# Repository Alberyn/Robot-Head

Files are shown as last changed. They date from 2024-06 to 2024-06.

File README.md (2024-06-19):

# Robot-Head
### Исследование
**Цели и задачи** - Проектирование насадки на роборуку Omron tm5-700.
Перед нами была поставлена задача проектирования, создания и симуляции насадки для роборуки. В процессе поисков вариантов и согласования идей с преподавателем, итоговый вариант представлял выполнения "кукушки" как в настенных часах. В процессе поиска вариантов внешнего вида и выполнения в интернете, было выбрано стандартное исполнение с выступающей птицей из-за дверок.

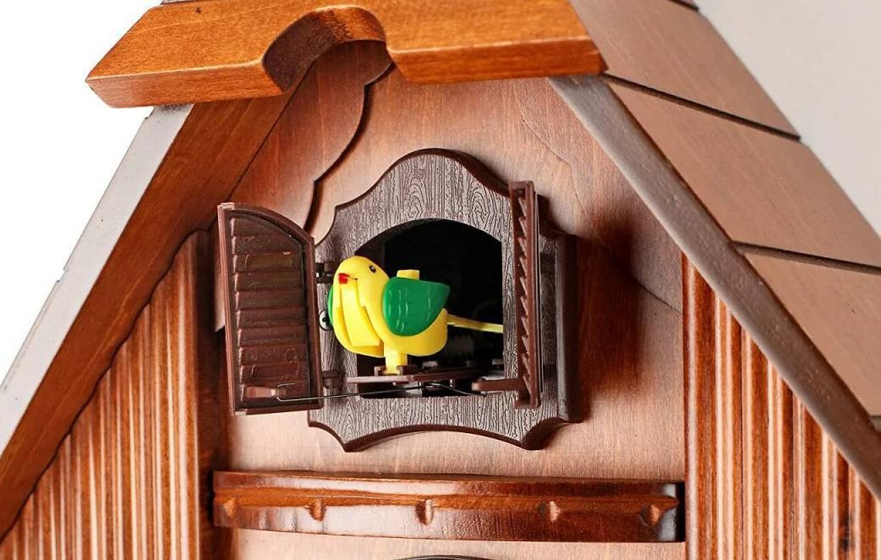
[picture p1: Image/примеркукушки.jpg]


В ходе исследования была выбрана концепция максимальной стандартизации и разбиения деталей на составляющие. Таким образом в случае неисправностей деталей, появления новых идей, влекущих изменение конфигурации сборки, время и количество изготавливаемых деталей заново было бы минимально. Данная концепция неизбежно влекла за собой ухудшение и/или игнорирование внешнего вида насадки.

Основой для насадки был выбран корпус квадратной формы из фанеры, так как соединение пазами не предоставляла достаточной прочности конструкции, соединения с использованием клея шли вразрез концепции, было решено использовать уголки с винтовым креплением. 4 стенки из 6 были выполнены одинаково, а уголки в последствии также использовались как опоры для перегородки с направляющей "кукушки". Для удобства крепления сборки на «руку» компоненты пришлось опустить ниже, соответственно сделать насадку выше, но это позволило выполнить разделение управляющих компонентов с питанием и движущих частей.

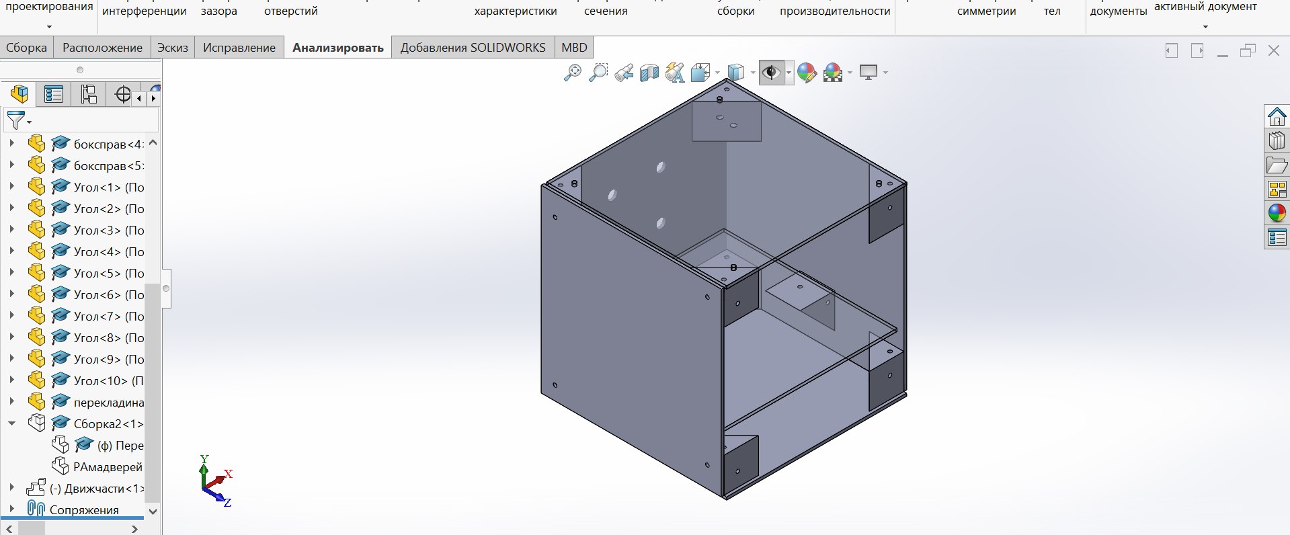
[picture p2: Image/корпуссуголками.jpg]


Для движения птицы использовалась зубчатая передача, была спроектирована система из направляющей, шестеренки, основания для утки, петель, дверок и рамы дверок, чьи модели можно найти в папке CAD.

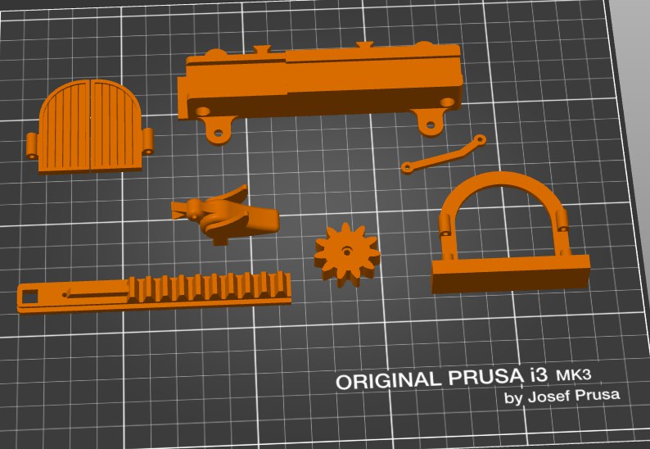
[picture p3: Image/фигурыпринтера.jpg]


В качестве системы для управления и движения птицы была выбрана система с пультом управления и написана управляющая программа:

```C++
#include <IRremote.hpp>

#define IR_BUTTON_OK 28
#define IR_RECEIVE_PIN 3
#define SPEED_1      5 
#define DIR_1        4
 
void setup(){
  Serial.begin(9600);
  IrReceiver.begin(IR_RECEIVE_PIN);
  for (int i = 4; i < 8; i++) {     
    pinMode(i, OUTPUT);
  }
}

void loop(){
   if (IrReceiver.decode()) {
      IrReceiver.resume(); // Enable receiving of the next value
      Serial.println(IrReceiver.decodedIRData.command);
      int command = IrReceiver.decodedIRData.command;
      
      switch (command) {
        case IR_BUTTON_OK: {
          digitalWrite(DIR_1, LOW); // set direction
          analogWrite(SPEED_1, 120); // set speed
          delay(600);
          analogWrite(SPEED_1, 0);
          delay(2000);
          analogWrite(SPEED_1, 120);
          digitalWrite(DIR_1, HIGH);
         // ждём одну секунду
          delay(600);
          // выключаем первый мотор
         analogWrite(SPEED_1, 0);

          break;
        }
      
      }
  }
}
```

В коде нет отсчета для проигрывания движения, оно выполняется после нажатия на кнопку, так как мне не нравится идея диктовки временем, когда случится какое-то событие, хотелось хотя бы в проекте самому решать, когда настанет этот момент.

**Используемое оборудование и программы**: плата Arduino Uno, драйвер Motorshield, блок питания, "моторчик", сенсор ИК излучения, провода, винты М3-8, 3D-принтер Prusa i3 MK3, Лазерный станок GCC Spirit GLS100,  SolidWorks, CorelDraw

**Методы изготовления**: Для корпуса и перекладины было выбрано использование фанеры и его вырезание на лазере (про существование акрила было забыто), уголки и прочие составляющие "кукушки" (птица, направляющая, петли, дверки итд) было решено создать на 3Д принтере, благодаря их относительно малому размеру наибольшее время печати было 28 минут на скорости 100%.

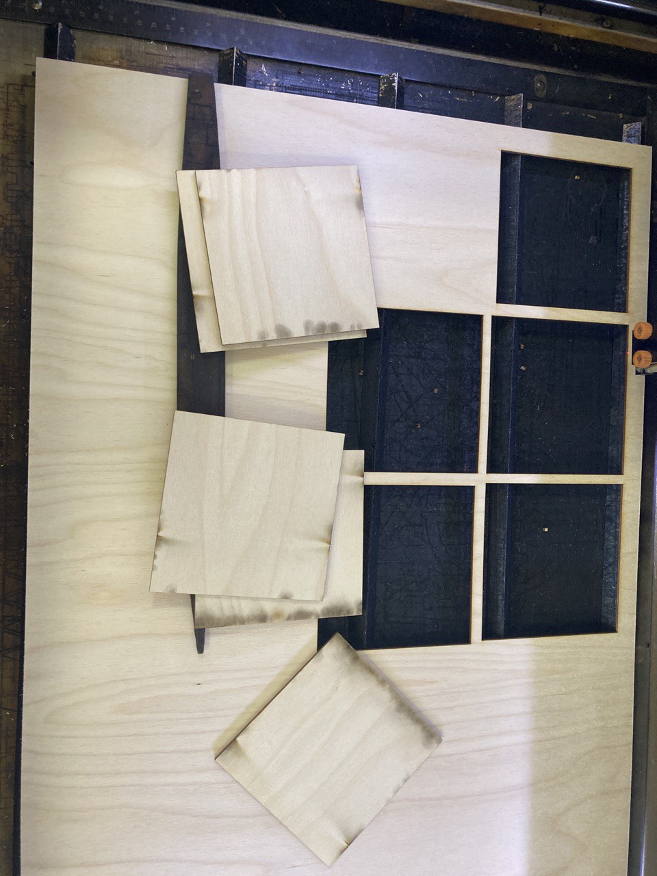
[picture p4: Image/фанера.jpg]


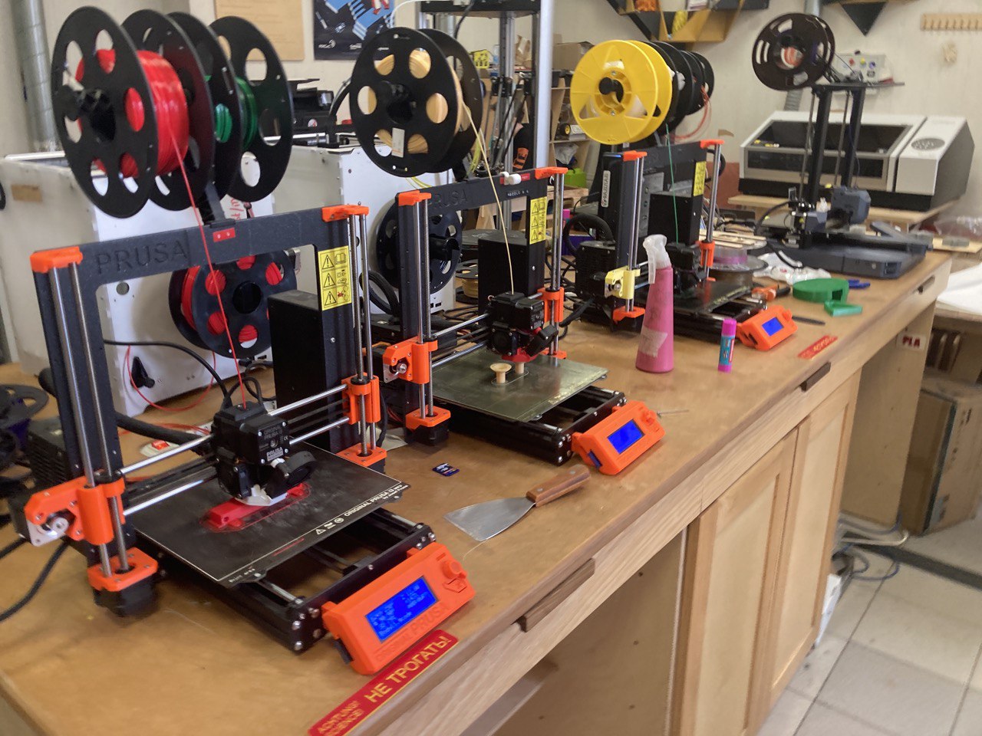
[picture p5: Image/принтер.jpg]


Общая сборка как и все прочие детали были выполнены в программе SolidWorks

### Производство
В ходе изготовления сначала была выполнена наладочная партия деталей и было выявлено ряд недочетов: недостаточный диаметр отверстий в уголке, неточное расположение отверстий в корпусе и непродуманное расположение проводов. Благодаря выбранной концепции, ошибки были быстро выявлены и исправлены, что не сильно сказалось на графике производства

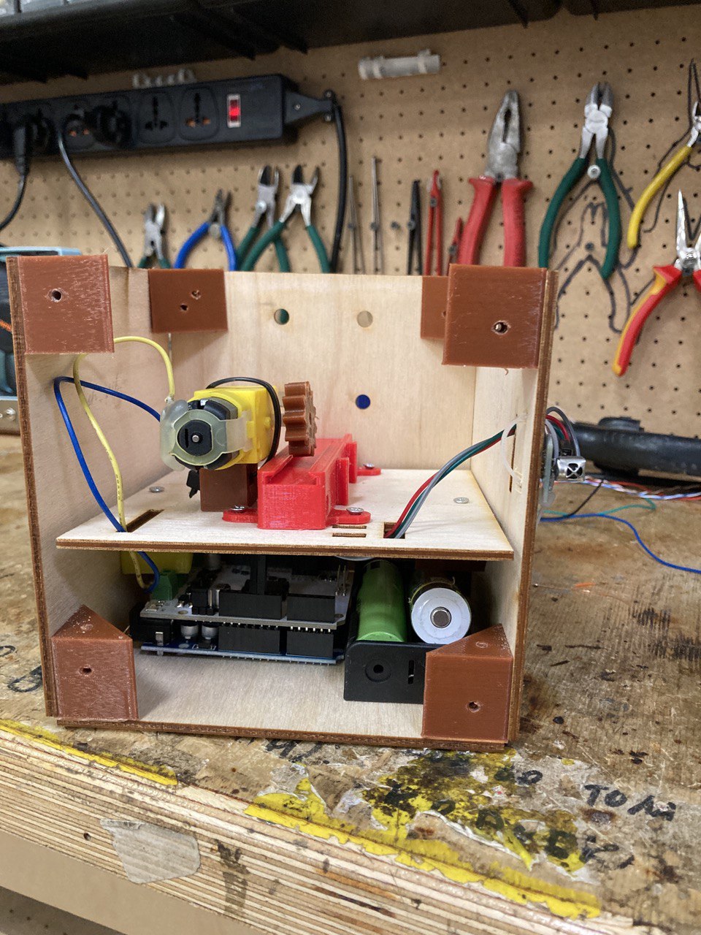
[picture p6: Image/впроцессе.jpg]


На рисунке выше представлена сборка основных напечатанных и всех электронных деталей сборки. В перегородке (на котором закреплен мотор и направляющая) были выполнены отверстия для прохождения проводов моторчика и проводов сенсора сигналов, который закреплен на внешней стороне корпуса.

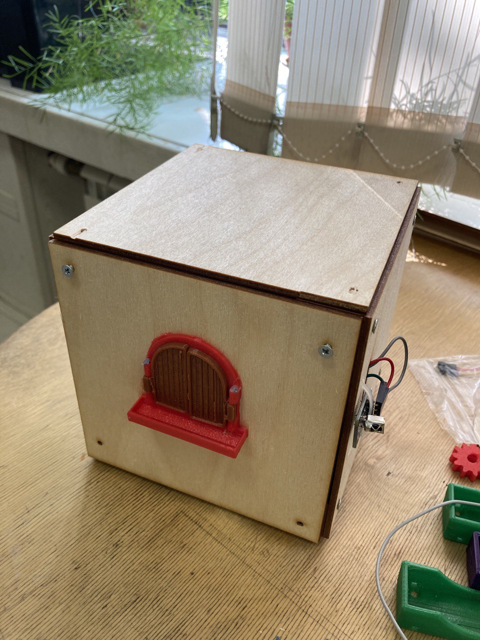
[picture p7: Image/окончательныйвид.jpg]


### Тестирование

GIF симуляция работы манипулятора:
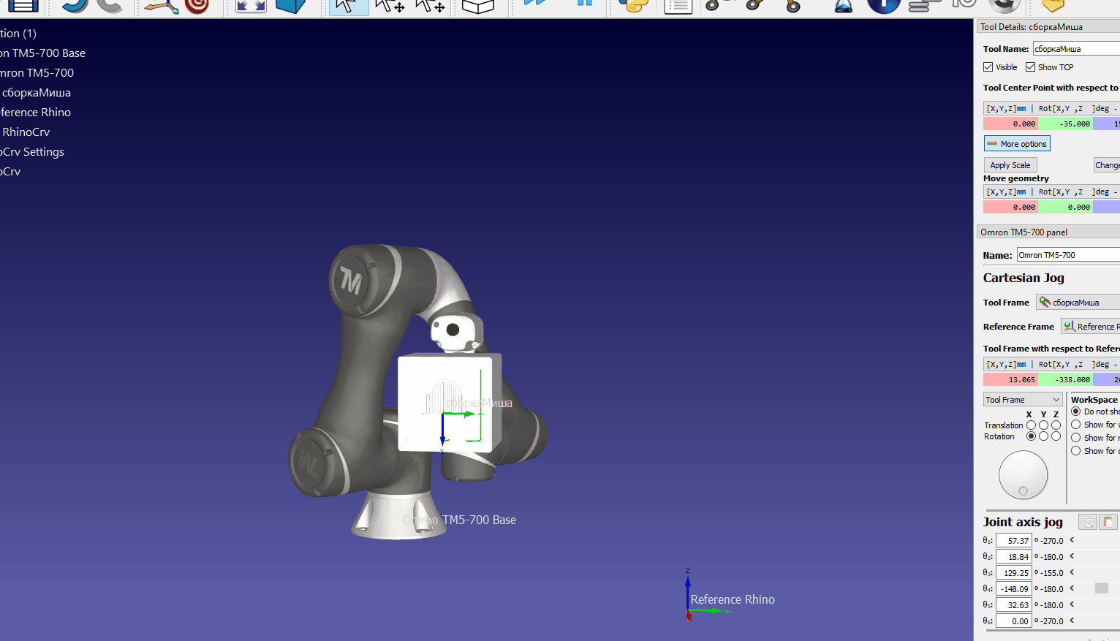
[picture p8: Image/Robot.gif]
Симуляция


Видео работы насадки и манипулятора:
[Презентация

## Недочеты
 1. Из-за выбранной концепции был отброшен вопрос эстетического вида и дизайна в целом
 2.	Недостаточная фиксация мотора в сборке из-за чего движение механизма не может гарантироваться постоянно. Но появляется вопрос с созданием дополнительного механизма для подвода и отвода шестеренки к зубчатому основанию
 3.	Из-за чувствительности сенсора и кнопки на пульте управления, иногда бывает двойное повторение программы

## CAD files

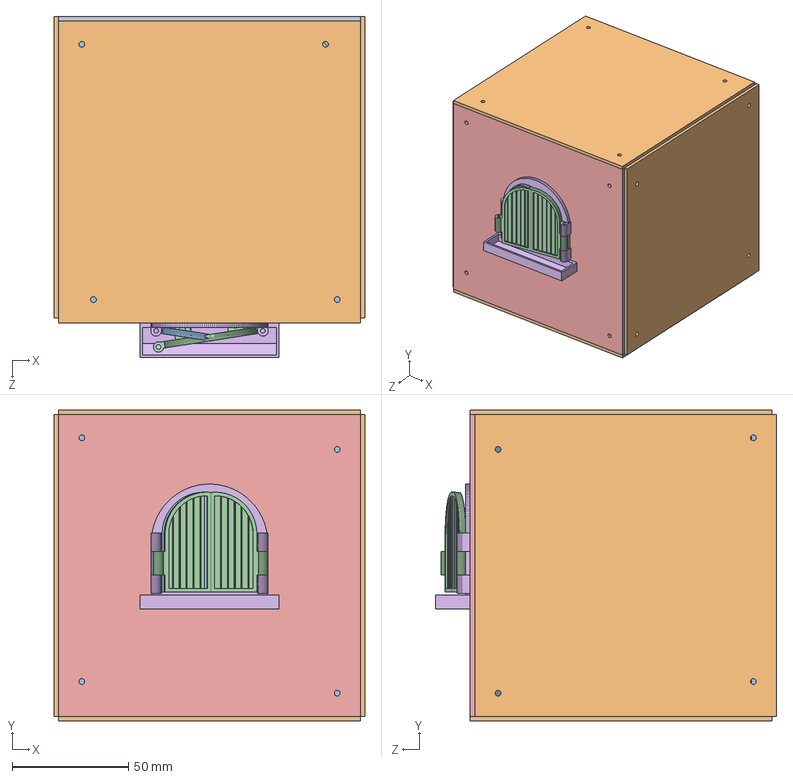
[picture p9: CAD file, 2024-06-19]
CAD/Сборка корпуса.SLDASM
134.0 x 134.0 x 147.0 mm
Задняя стенка
боксправ x 4
Угол x 10
перекладина
Передняястенка
РАмадверей
Зубчатая передача
Направляющая
Птица
пендель x 2
Дверцыпосле определения
Праваядверь

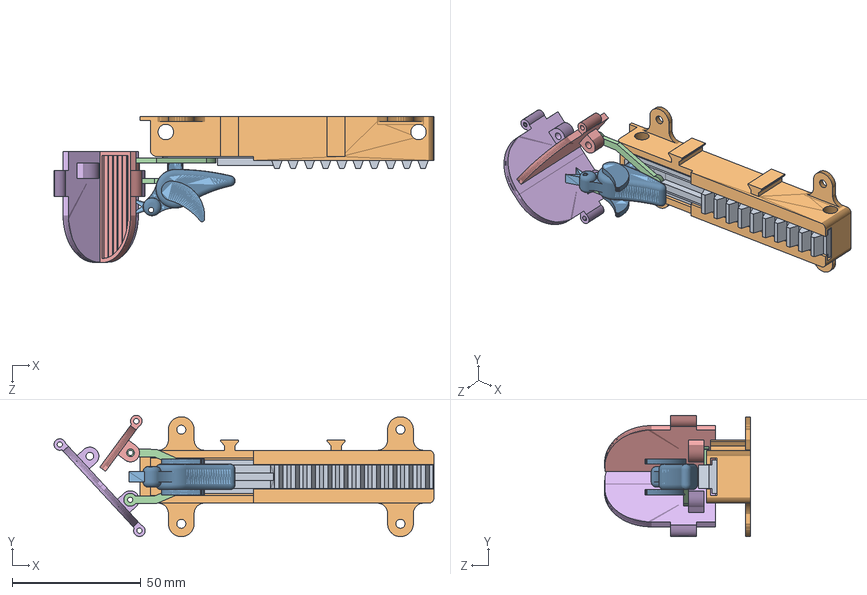
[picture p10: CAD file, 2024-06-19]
CAD/Движчасти.SLDASM
147.4 x 47.1 x 56.6 mm
Зубчатая передача
Направляющая
Птица
пендель x 2
Дверцыпосле определения
Праваядверь

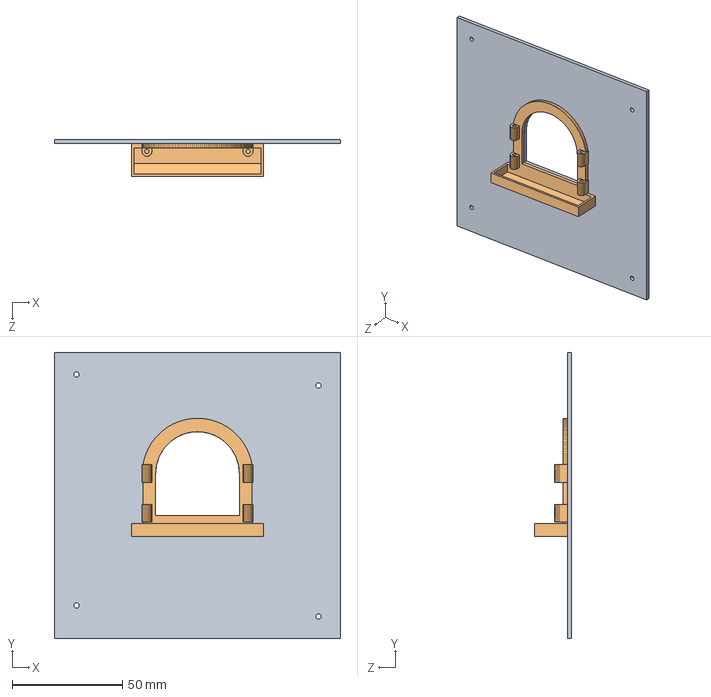
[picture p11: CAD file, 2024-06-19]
CAD/Сборка2.SLDASM
130.0 x 130.0 x 17.0 mm
Передняястенка
РАмадверей

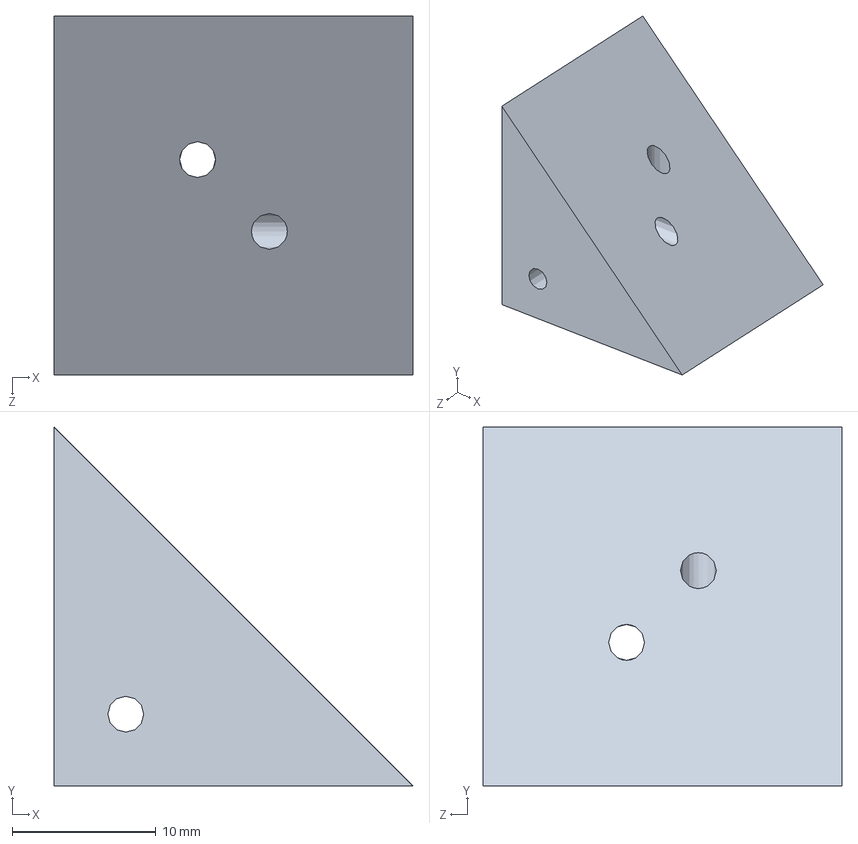
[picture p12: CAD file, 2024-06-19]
CAD/Угол.SLDPRT
25.0 x 25.0 x 25.0 mm

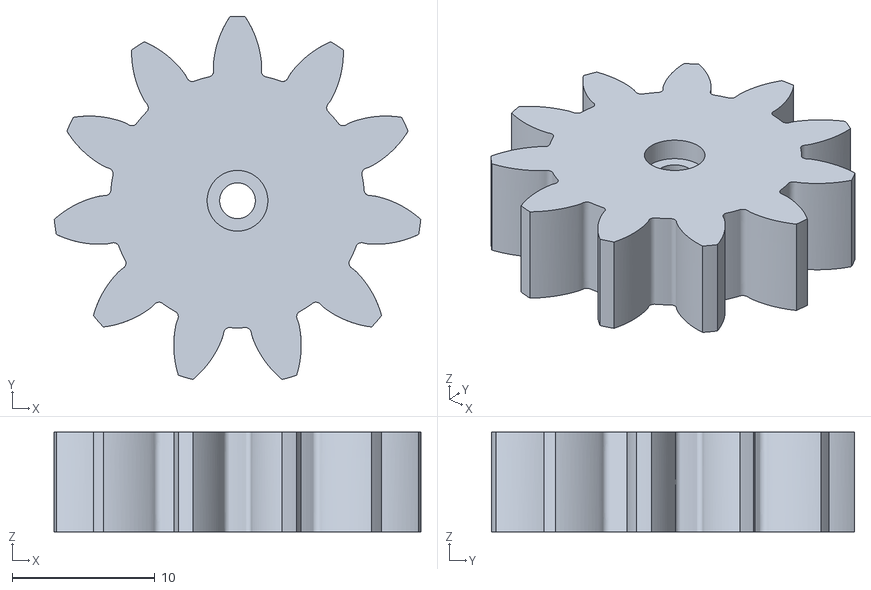
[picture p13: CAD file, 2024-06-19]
STL/KK_pinion2.stl
25.7 x 25.4 x 7.00

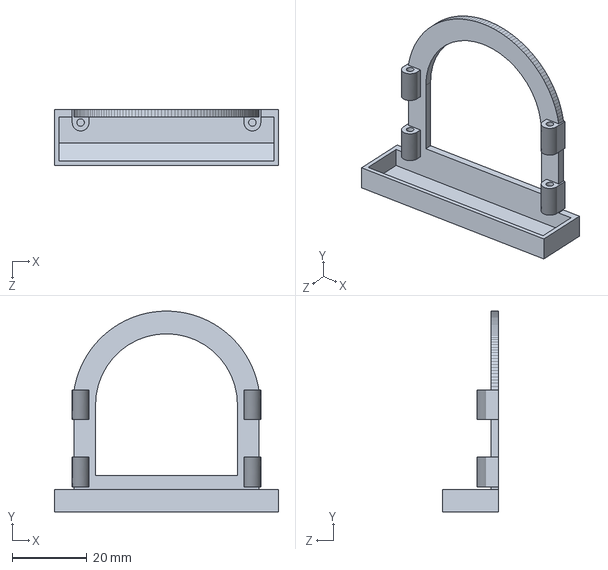
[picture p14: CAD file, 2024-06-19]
CAD/РАмадверей.SLDPRT
60.0 x 53.8 x 15.0 mm

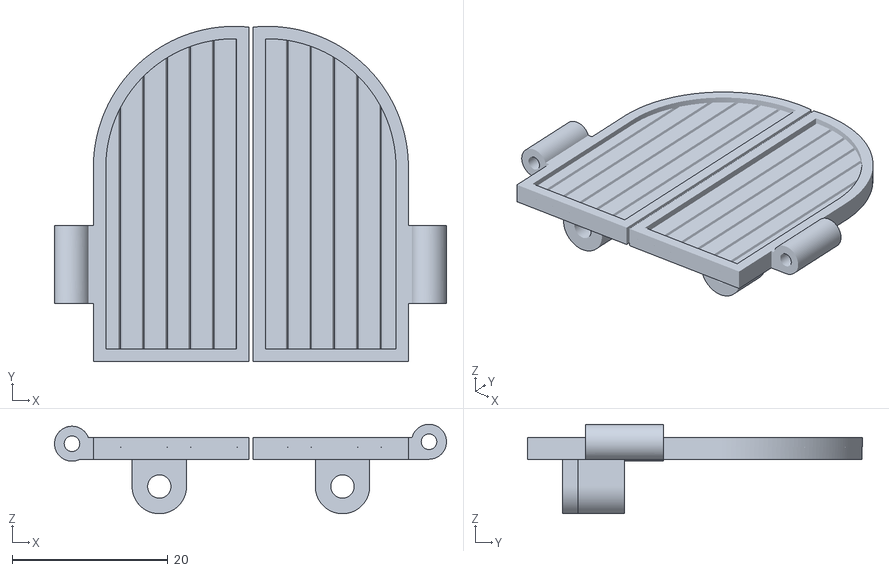
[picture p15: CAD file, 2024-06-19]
STL/KK_luiken.stl
50.4 x 43.1 x 11.5

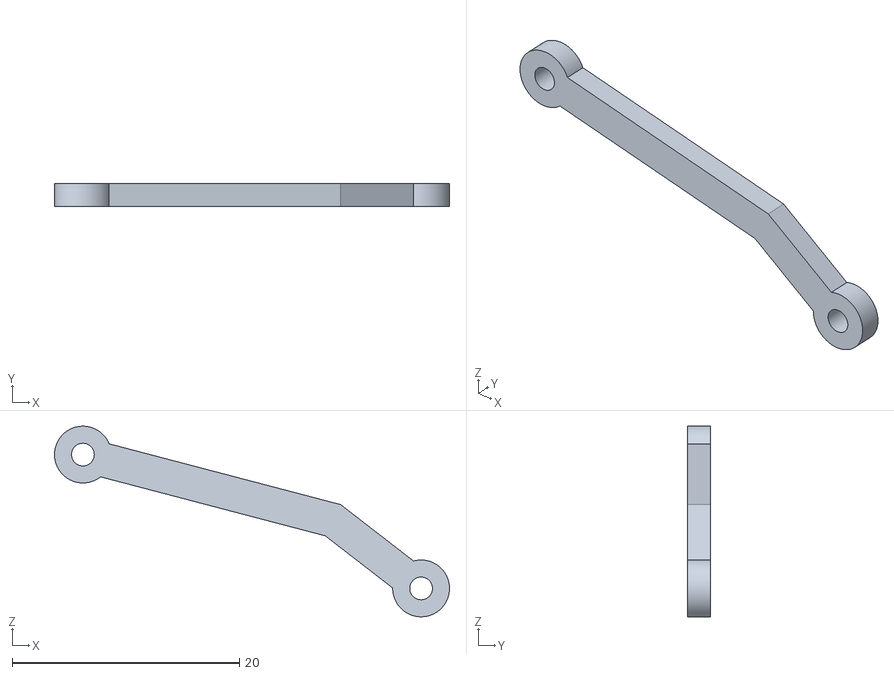
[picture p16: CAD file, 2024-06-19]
STL/KK_pendel2.stl
34.8 x 2.00 x 16.8

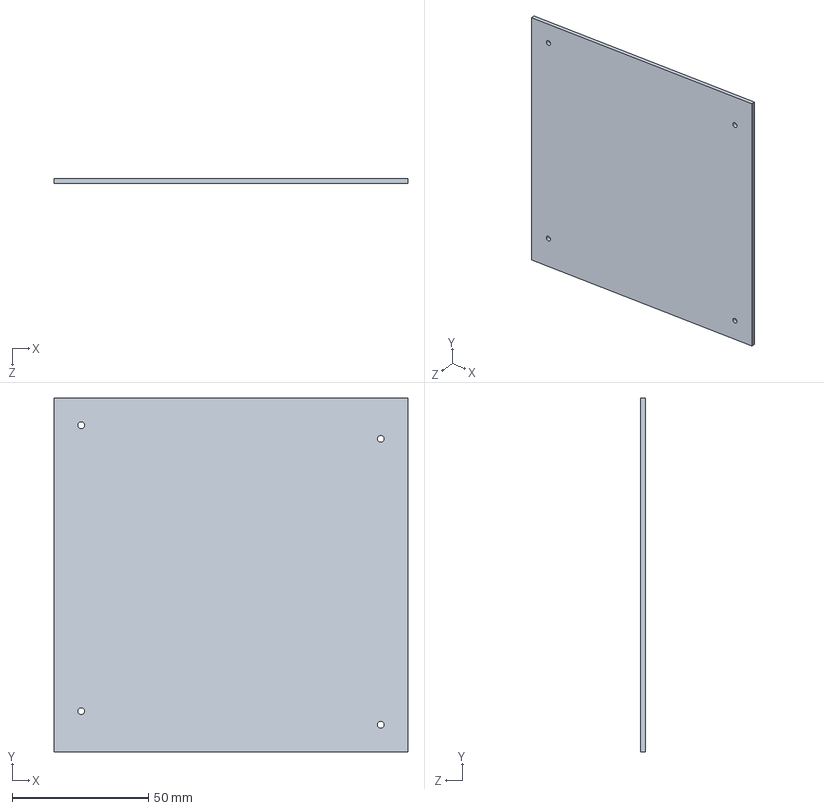
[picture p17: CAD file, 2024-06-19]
CAD/боксправ.SLDPRT
130.0 x 130.0 x 2.00 mm

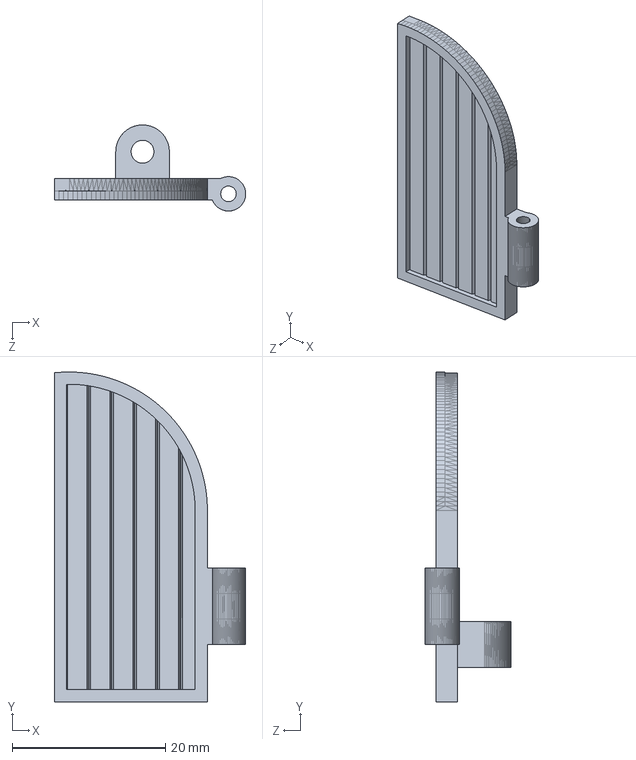
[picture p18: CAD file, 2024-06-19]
CAD/Праваядверь.SLDPRT
25.0 x 43.1 x 11.2 mm

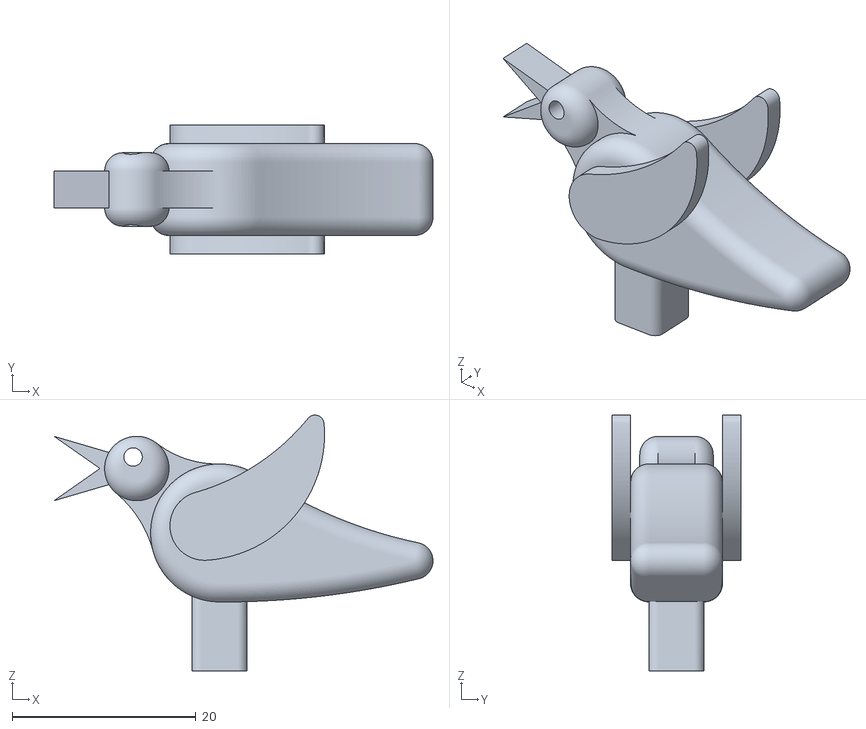
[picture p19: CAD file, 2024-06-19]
STL/KK_bird.stl
41.2 x 14.0 x 27.8

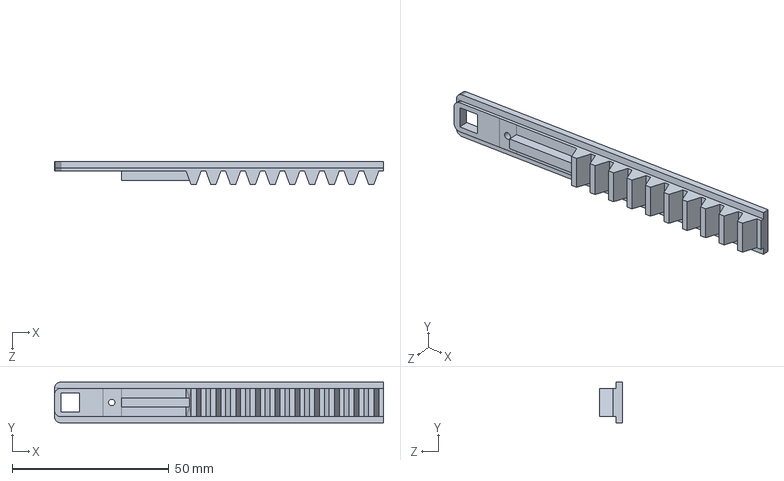
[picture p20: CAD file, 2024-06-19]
CAD/Зубчатая передача.SLDPRT
105.0 x 13.0 x 7.25 mm

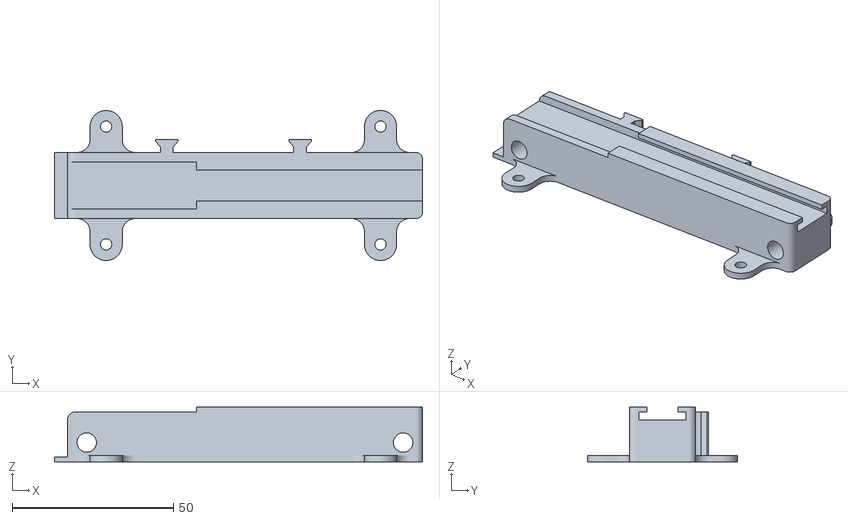
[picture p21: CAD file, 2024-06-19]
STL/KK_body.stl
114.0 x 46.5 x 17.0

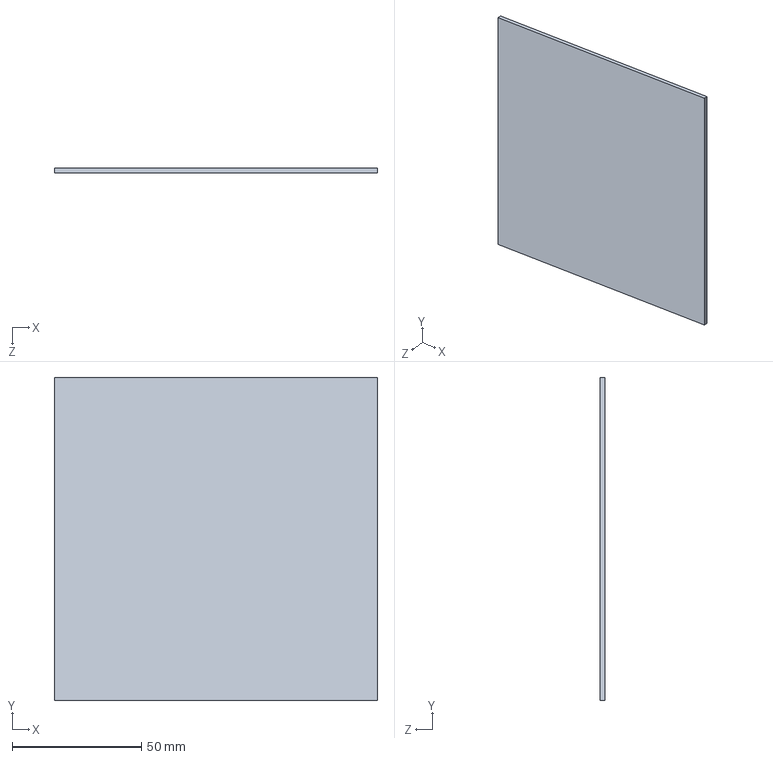
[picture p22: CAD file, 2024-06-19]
CAD/перекладина.SLDPRT
125.0 x 125.0 x 2.00 mm

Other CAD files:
CAD/Дверцы.SLDPRT
STL/KK_luikframe.stl
CAD/РАмадвере.SLDPRT
CAD/пендель.SLDPRT
CAD/Дверцыпосле определения.SLDPRT
CAD/Задняя стенка.SLDPRT
CAD/Передняястенка.SLDPRT
STL/Сборка корпуса.STL
